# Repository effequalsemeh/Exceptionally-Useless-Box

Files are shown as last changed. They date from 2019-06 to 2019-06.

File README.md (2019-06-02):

# Exceptionally-Useless-Box
All files related to building the Exceptionally Useless Box

See demonstration of the device working here: https://youtu.be/8gKpCouH2lw

There is only a rough guide for setting this thing up, and it's from the project report that was generated for this. Look at Documentation/MECH-457, Project Report, Reduced. I will upload a better schematic and assembly guide later on as time permits.

To-Do:
1. Upload schematic after drawing in Eagle/KiCad
2. Create a BOM
3. Upload a guide on assembly

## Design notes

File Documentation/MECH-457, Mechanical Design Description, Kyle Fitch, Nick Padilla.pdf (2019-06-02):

## Mechanical Design Description for the MECH-457 Project

### Exceptionally Useless Box

Note that a Solidworks model should be supplied with this document that these words are in reference to.

The project is housed in a 1/8th inch, laser-cut enclosure that facilitates mounting points for a toggle switch, ultrasonic proximity sensor, two different servo-arm assemblies, and hinged doors from which arms may egress. Hinging of the doors is accomplished with flush-mount piano hinges. Each servo assembly features a mount for connecting to the servo and chassis. The servo mount also features a bolt for a fixed pivot point where a 5-bar linkage (the arm) connects to. The servo mount provides limited adjustability in xyz directions for alignment purposes.

Power is supplied by a battery pack, which will be adhered to the inside of the enclosure using adhesivebacked hook-and-loop tape. Similarly, the breadboard for connecting the electronics is also adhered to the inside of the enclosure with the built-in adhesive backing where clearance allows. Lastly, a power switch is panel-mounted on the bottom for turning the device on and off.

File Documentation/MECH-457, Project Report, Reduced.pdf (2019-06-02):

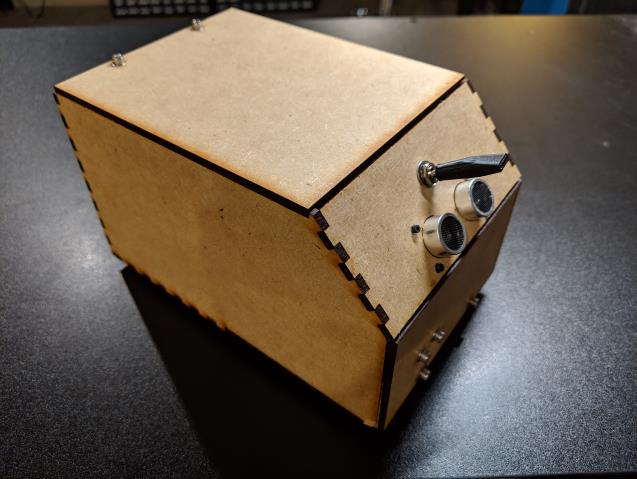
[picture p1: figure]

# Exceptionally Useless Box

Kyle Fitch

Nick Padilla

MECH 457/857

5/1/19

## Summary of Project

There is a novelty toy called a “useless box” where a box features a mounted switch that the

user toggles. Upon toggling the switch, something comes out of the box to toggle the switch back to the

original position. The goal of this project was to make an exceptionally useless box. In order to do this,

the user should not even get to toggle the switch in the first place. Therefore, the box needed to watch

for the user’s hand approaching and preemptively toggle the switch when the hand gets close enough

followed by the usual sequence of resetting the switch as in the original useless box design.

To detect the hand, the device features an ultrasonic sensor connected to an Arduino Pro Mini.

The microcontroller uses this input as a way to detect the proximity of the hand and translate that

distance into rotating a servo. In doing this, the servo motion “follows” the hand as it approaches or

backs off. Connected to this servo is an arm made up of a 5-bar linkage that when fully extended can

toggle the switch and similarly fully retract into the box. A second servo with another arm serves the

purpose of resetting the toggle switch once it has been engaged by the other arm.

The team hoped that such a simple concept would leave plenty of time to execute and perfect

complete mechanical and electrical designs with well-performing code. Unfortunately, with the

complexity involved in the 5-bar linkages, iterating the mechanical design took a large portion of the

semester. Since the mechanical design needed to be complete before tuning the coding, the

performance of the device was not able to be honed. However, the device in its present state meets our

expectations in its functionality and aesthetic appearance. Early on in the project, having the motion of

the servo follow the distance measurements made by the sensor was intended to be controlled with

PID. Currently, this function is performed instead by a mapping function and rolling average filter.

Future testing will be performed to implement PID control for much faster response and a reduction in

the jittery motion sometimes brought on by the sensor. Lastly, it would be ideal to make a circuit board

to get rid of the breadboard electronics which will reduce the amount of wiring inside the device and

thus reducing noise in the system.

## Table of Contents

Step 1 – Component Validation
Step 2 – Sensor wiring
Step 3 – Servo wiring
Step 4 – Toggle switch wiring
Step 5 – Microcontroller power wiring
Step 6 – Electronics testing
Step 7 – Mechanical design
Step 8 – Finished Project

### 1Component Validation

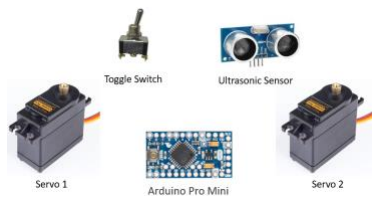
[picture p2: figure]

Component selection was straightforward in that they were already defined when the concept of the project was determined. It was known that two servos, one ultrasonic sensor, a toggle switch, microcontroller, power switch, and batteries would be necessary. An Arduino Pro Mini was chosen for the microcontroller since it was on hand through the lab materials of the MECH-457 course. The ultrasonic sensor that was selected was an HC-SR04 module, which are plentiful and cheap, and were curated through Amazon. The power switch and battery packs (for AA batteries) were already on hand and were used for the project. These components worked well and were used in the final project.

Originally, an SG90 micro servo was used in the design to drive the arms due to their small size. This proved to be a mistake as it not only had too low of torque, but the nylon servo horns that it came with were difficult to join the arms to. After observing this, larger servo motors were ordered that included standard teeth (25T) for the servo horn. These motors had 15 times the amount of torque that the micro servos had, so was clear that that problem would be solved. Because of the 25T tooth profile on the servo meant that a special, metal servo horns could be used to join the arms using threaded holes in the horn. This ended up being the perfect solution for converting the torque of the motor to the arms.

On the subject of torque, a larger toggle switch was originally purchased for having a longer lever to solve some clearance issues in the kinematics of the arms. Unfortunately, the force required to flip the toggle switch was very high and the housing behind the lever of the switch (the part that is hidden inside the enclosure) was too bulky and caused many different clearance issues. A mini toggle switch was then purchased which had a lower force to flip and was much smaller in size. A 3d printed part was designed to slip onto the lever for increasing the length of the lever as well, which lowered the force needed to toggle the switch even further.

The enclosure was intended to be laser cut from 0.125” material and would be appropriate regardless of the type of material (that can be cut with a low power laser) since the joints would be bolted connections and finger joints with an adhesive. For this project, MDF was used because it was low in cost and easy to cut on the laser with reliable, flat surfaces that did not warp during the manufacturing process. However, Delrin was used for the linkages for their high strength and rigidity. Delrin also cuts well on the laser, but with larger parts, it can have some warping. This was not an issue, however, since the linkages were quite small.

The mounts of the servo motors and arm were originally made from MDF, but after prototyping, it was obvious that it would not be rigid enough, so Delrin was also used for these parts as well. The pins that were used for joining the arm linkages were machined from 1/8” stainless rod stock since they were non-standard lengths. Retaining the linkages on the pins were friction-based snap ring clips, which allowed for adjustment in the amount of play between the linkages. Another benefit to using Delrin for the linkages was the material’s low coefficient of friction, which kept the linkages from binding throughout their motion.

All fasteners involved in the project were determined during the modeling process and ordered from McMaster-Carr when the design was ready. Finally, piano hinge material was used to join the top and front “doors” to the enclosure.

### 2Sensor Wiring

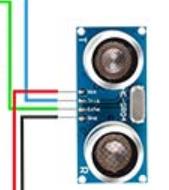
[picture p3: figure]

Wiring an ultrasonic sensor is straightforward and is made even easier with a datasheet provided by the manufacturer. There are 4 pins: input voltage (VCC), ground (GND), trigger (TRIG), and echo (ECHO). Voltage from the “RAW” pin of the microcontroller was connected to VCC. GND on the sensor was connected to the GND of the microcontroller. TRIG and ECHO pins needed to be connected to any digital pin, which for this project were pins 6 and 7, respectively.

Most manufacturers of the HC-SR04 also provide the equation that is needed to calculate the distance from the readings of the sensor. So, it was not necessary to determine this ourselves.

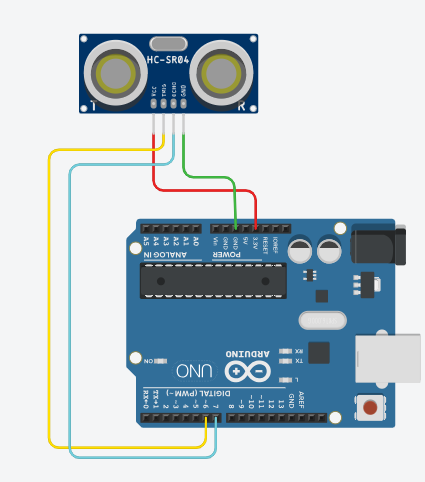
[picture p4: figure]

### 3Servo Wiring

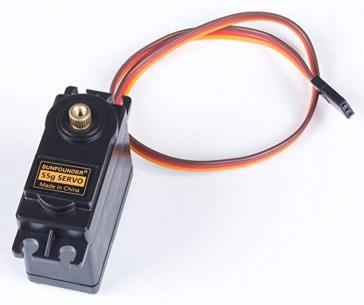
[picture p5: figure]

Servos typically have just three leads to connect; input voltage, ground, and signal. The respective wires will vary from motor to motor, so consulting the datasheet was be necessary to determine which lead is what. For this project, the red wire was Vin, the brown wire was GND, and the yellow wire was signal. It was important to connect the Vin and GND wires to a separate power supply than the one that powers the microcontroller. This avoided frustrating noise issues that are difficult to troubleshoot. The magnitude of the input voltage also varies from motor to motor and must be sought out from the datasheet. For this motor, 6V were required with up to 2A of current. So, a battery pack with four AA batteries connected in series were connected to the Vin and GND wires of the servo motors. The signal pins for each motor were then connected to a PWM-enabled digital pin on the microcontroller (pin 10 for the bottom arm servo, pin 11 for the top arm servo). A rocker switch was also connected between the series circuit of the batteries and servos to control when the motors were given power.

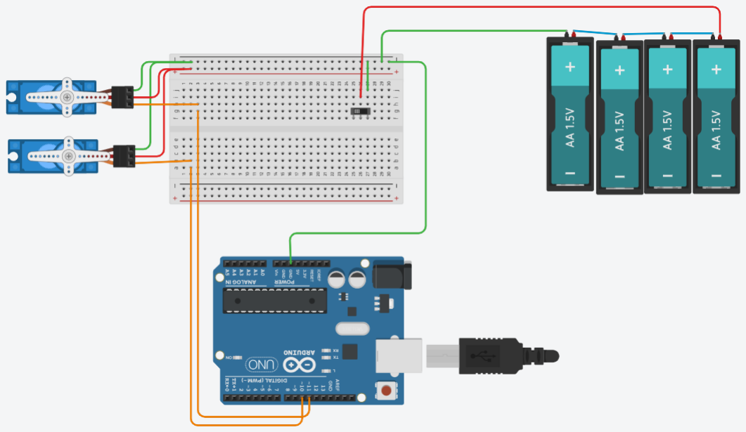
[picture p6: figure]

### 4Toggle Switch Wiring

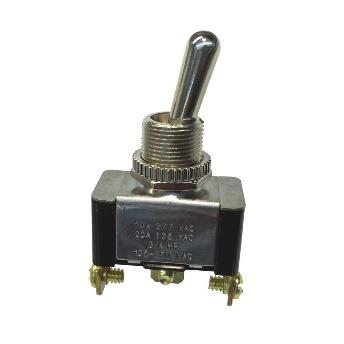
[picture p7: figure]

The toggle switch that was to be flipped back and forth by the device was connected from a digital pin (pin 5 for this project) to the GND pin of the microcontroller. Since the switch would be normally open, a pull-up resistor was required from the digital pin to the 3.3V output of the microcontroller. The value of this resistor was mostly arbitrary barring abnormally high or low resistances. A 10 kΩ resistor was used for this project.

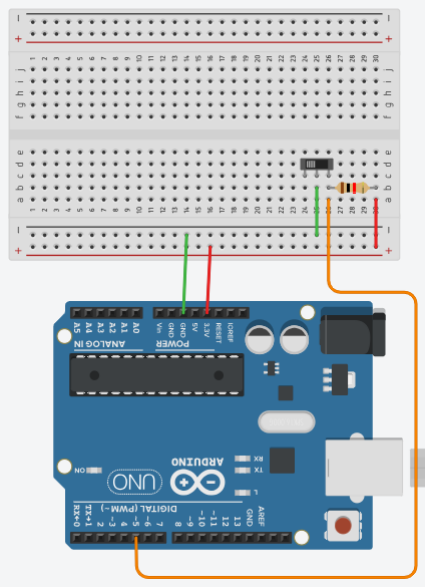
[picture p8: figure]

### 5Microcontroller Power Wiring

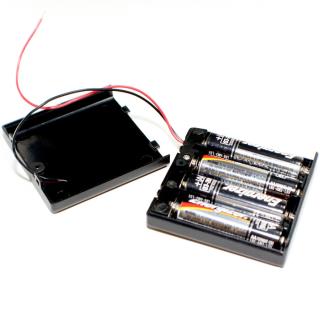
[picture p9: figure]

The microcontroller needed to be supplied with a separate power supply from the servo motors as indicated in step 4. From the datasheet, the input voltage for the microcontroller would need be from 3.3V to 12V. So, another 4 AA batteries were placed into a battery pack whose leads were then connected to the RAW pin (positive side of battery terminals) and GND pin of the microcontroller.

As was done before, another switch was placed between the positive lead of the battery pack and the RAW pin. This would allow for independent power cycling of the microcontroller and sensor so that the device could be unpowered when not in use. It was also useful to be able to power the microcontroller without the servos activated so that if code that was previously uploaded and caused crashes, it could be safely rectified.

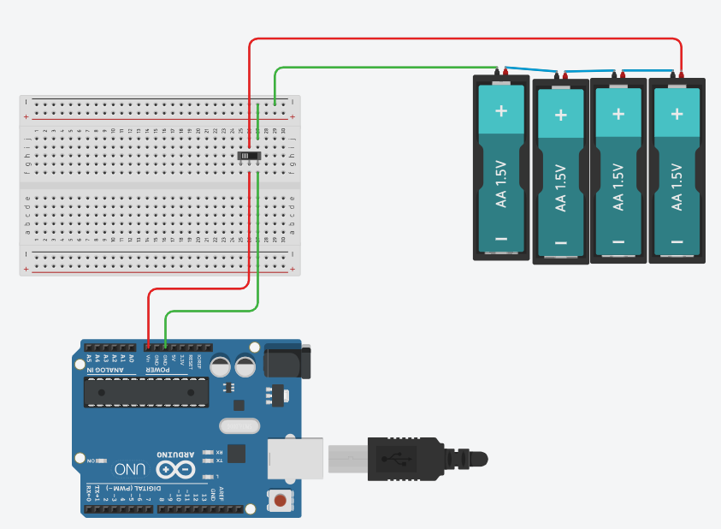
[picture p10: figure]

### 6Electronics Testing

With the electronics connected, they were tested before
assembling into the enclosure itself. Prototyped code was uploaded

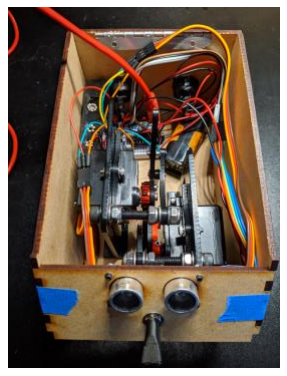
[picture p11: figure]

to the microcontroller using the Arduino IDE. It was important to ensure that the correct processor is selected before uploading. This caused for some headache when initially working with this board. For this project, we used the 3.3V 8 MHz version of the Arduino Pro Mini.

With the code uploaded, we pointed the sensor in a direction with a lot of space. Some noise was heard from the servos when the program loads, indicating that they were energized. Then, a hand was placed in front of and a couple feet from the sensor and slowly approached the sensor. The bottom then rotated as the hand became closer to the sensor. When the hand was close enough, the servo suddenly moved, and both servos remained still thereafter. After flipping the switch one direction, the other (top) servo was observed rotating. After flipping the switch in the other direction, the top servo rotated once again. Finally, the bottom servo was again responding to input from the ultrasonic sensor.

### 7Mechanical Design

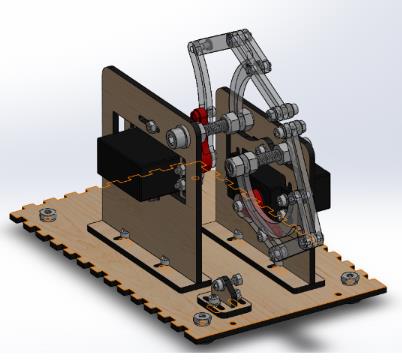
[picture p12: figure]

The most difficult part of the design in this project was being able to fit the servos as close to the switch as possible. Because the arms needed to contact the switch directly in line (such that they were both rotating or moving in the same plane), both servos could not be positioned in the same place with respect to the switch. To avoid this headache, one could simply position them in the same place yet separated along their axes of rotation far enough away to give clearance for the arms and at the end of either arm, a perpendicular piece to contact the switch lever with could be added. However, this would add a much larger torque to the linkages and rigidity issues will have arisen when attempting to make such a small form factor. It is this fact that there were two servos instead of one that made this project exceptionally challenging.

The mechanical design was begun by modeling the switch and fixing it in a position that was indicative to where it will be in the final design. Using circles as guides, the best combinations of lengths for the 5-bar linkage were experimentally determined until the end of the arm that meets the switch could fully retract into what would be the enclosure as well as extending a good amount of distance past the toggle switch so that flexure in the parts could be compensated for. This was where most of the time was spent in the design. It was important to give plenty of room for everything. The more that the size of the enclosure was limited, the more difficulty there was in designing the linkages. This process was done for the bottom arm only. The top arm was dependent on the physical size and shape of the bottom arm and required its complete model before designing the top arm linkage.

With the bottom linkage prepared, a mount that can hold the servo with adjustability in the translation of the servo in all three axes was modeled. Doing this allowed for adjustability in the actual prototype to make up for defects and ended up being extremely useful. The mount itself was the ground for the 5-bar linkage and allowed for adjustability in the positions of the two ground points with respect to one another. The mount was designed for rigidity where possible, knowing that a torque will be placed on the ground points.

Once an adjustable servo mount had been designed, the enclosure was modeled for affixing the mount, toggle switch, and ultrasonic sensor. The sensor needed to be positioned so that it is pointed where the user would be. It was important to not let the arms interfere with the sensor measurements as well. One thing that was not accounted for in our design was an angular adjustability in the ultrasonic sensor. While a 45 degree angle with respect to the surface that the device rested on worked, a lower angle would have resulted in better distance measurements since the hand tends to approach the device from an angle more directly in front of it, rather than above.

With the sensor and bottom servo arm mechanism mounted and fixed in place, the top arm to toggle the switch back was designed using the same procedure as was done with the bottom arm. It was critical to keep track of where the bottom arm will be during all points of its rotation so that the top arm can always perform without interference. A lot of time was spent here as well since the clearances for everything were very difficult to determine until complete models were made whose motions could be observed in an assembly to inspect for flaws.

Some way to retract the front door was also necessary. A tension spring was used for this project, but a torsion spring could have been used, but it was more trivial to find joinery that would easily accommodate the tension spring. The top door automatically closed by virtue of its own weight, so a return mechanism was not needed. A way to join the hinges to the enclosure and both doors was also be necessary. For this project, holes were drilled in the hinges and then bolted to their respective pieces. Modeling was also necessary for this feature as well because slots in the enclosure parts were needed for bolt clearances that
accommodated some tolerancing in the hinge’s position.

When designing the enclosure, enough room was needed to be made for not only the servo arm subassemblies, but also for the electronics. Room was accommodated for a mini breadboard with 2 battery packs and means for mounting the two power switches. Lastly, this project did not include an access panel for changing batteries, but would have been beneficial to include for the lifetime of the product when battery changes were needed.

Since the majority of the mechanical parts were to be laser cut, it was extremely useful to have the entire product modeled (excepting the microcontroller, breadboard, and wiring). In doing this, changes to the design could quickly be made, verified, exported to a laser job file, and fabricated. Modeling in this way was most likely critical to the success of this design because of the amount of iteration that was involved in prototyping.

When the parts were completely modeled, the prototype was assembled without the front and top doors attached. Some simple code to extend and retract each arm one by one was uploaded. While observing the motion of the links, adjustments were made to the servo mounts positions with respect to the toggle switch until both arms were reliably toggling the switch lever. At the same time, the exact angle limits of each servo were experimentally determined by adjusting their values in the code. When it was confirmed that the arms were completely retracted without striking each other and that both arms could flip the toggle switch, the doors were assembled and the hinges adjusted to allow the doors to completely close without interference. Similarly, tension on the spring of the return mechanism for the front door was adjusted by sliding the spring’s mounting point further away so that the front door would completely close.

### 8Finished Project

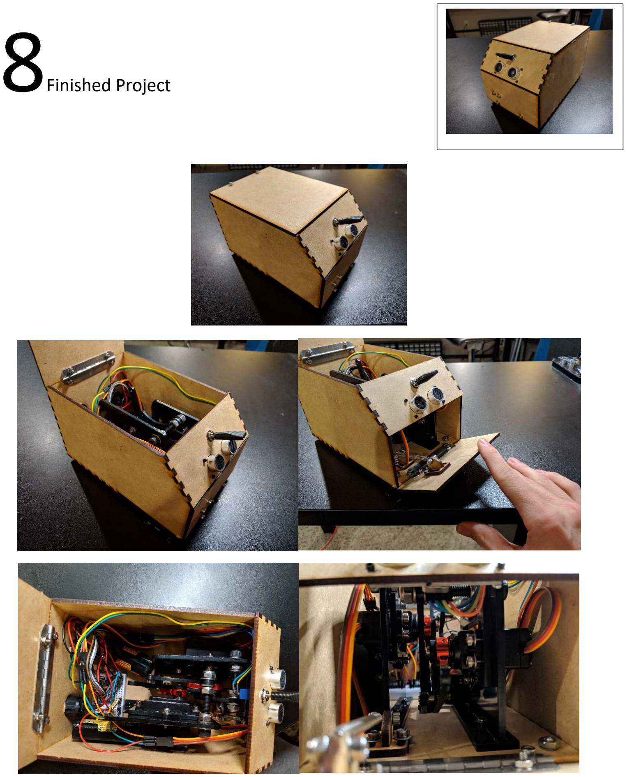
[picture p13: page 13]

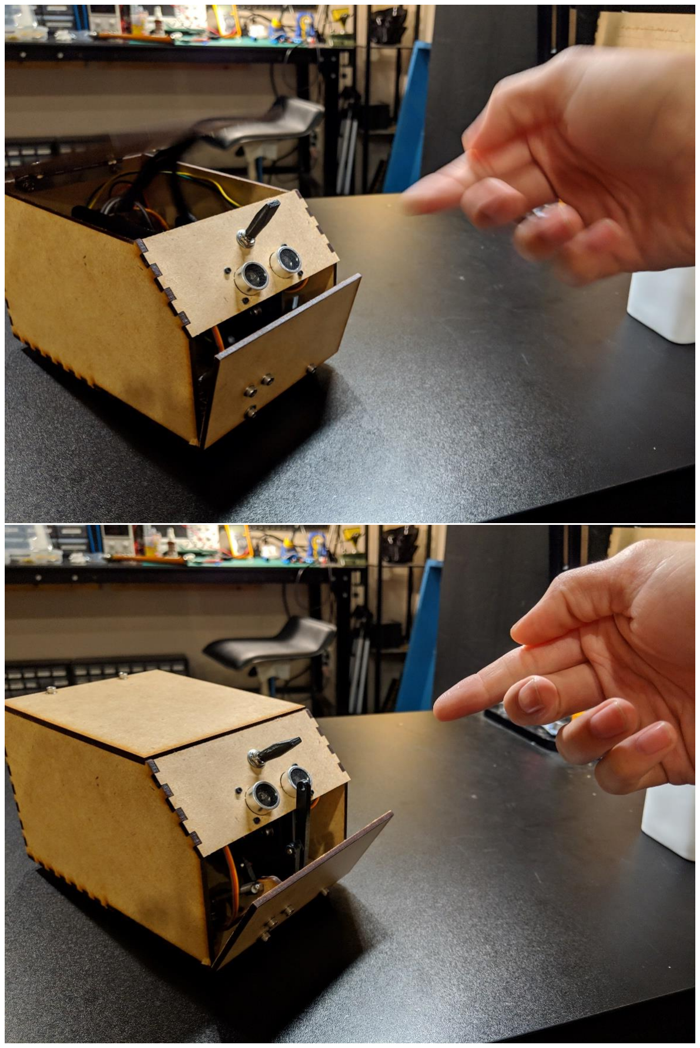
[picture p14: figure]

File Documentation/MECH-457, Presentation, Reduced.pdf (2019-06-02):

# Exceptionally Useless Box

## KYLE FITCH

## NICK PADILLA

# Motivation/Background

# This is a useless box

But it’s not really that useless…

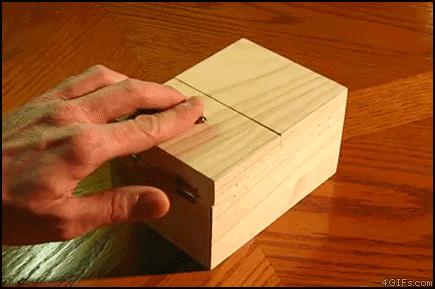
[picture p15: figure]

# HOW DO WE MAKE A BOX THAT IS EXCEPTIONALLY USELESS?!

# THE EXCEPTIONALLY USELESS BOX

Remove the interaction of the user with the box altogether
- The box flips the switch itself when a hand approaches
- Then the box flips it back like normal

Components:
- Arduino
- Ultrasonic sensor (measure distance of hand)
- 2 servos
- Toggle switch

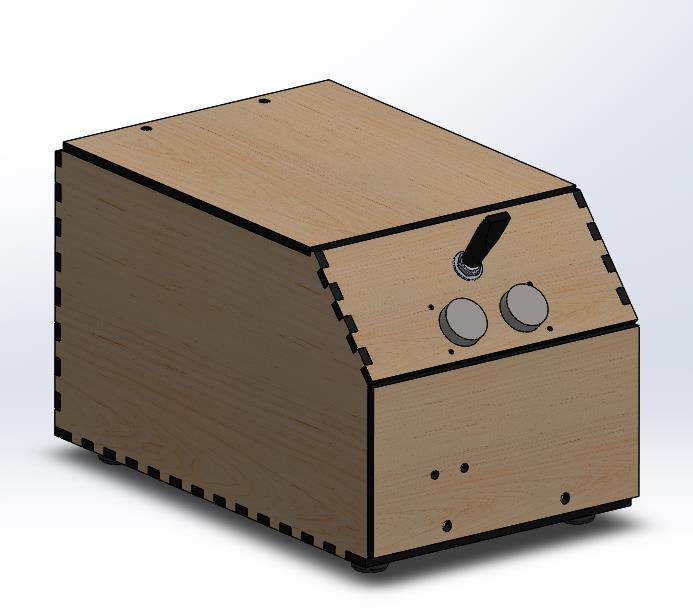
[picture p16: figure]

How can a robot have a purpose when you take it away?

# Calculation Components

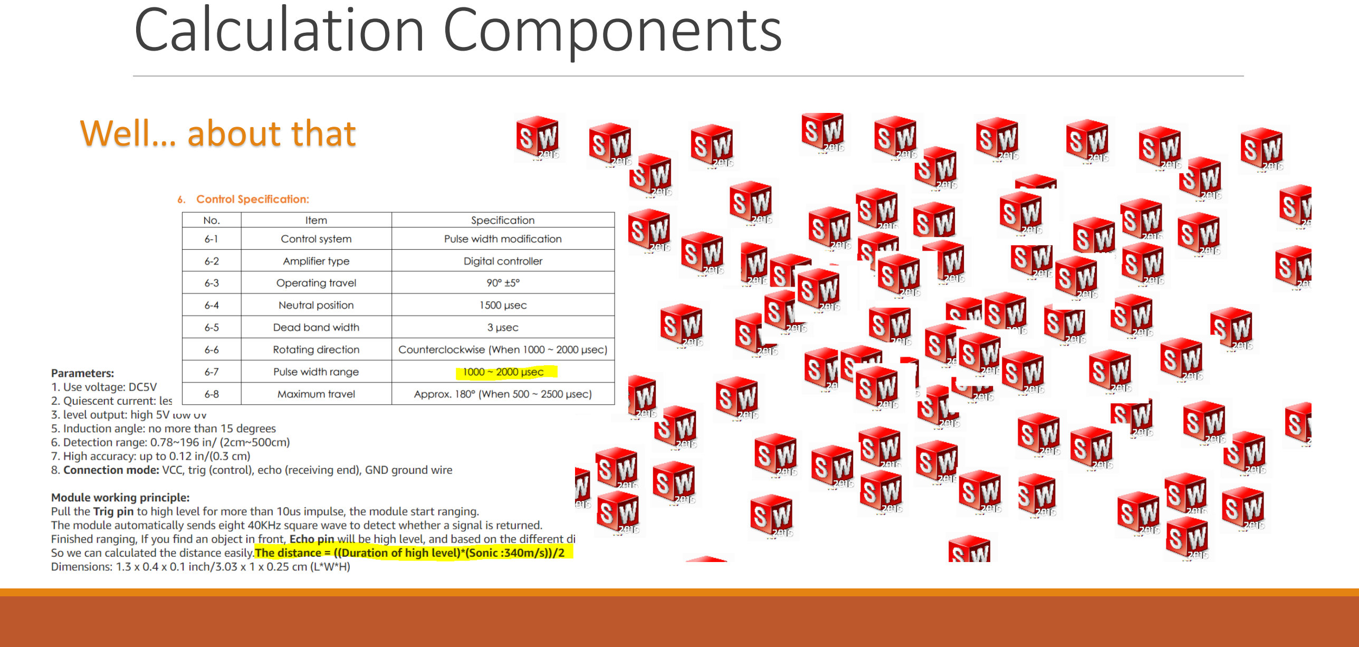
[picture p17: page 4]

## Well… about that

# Calculation Components (2)

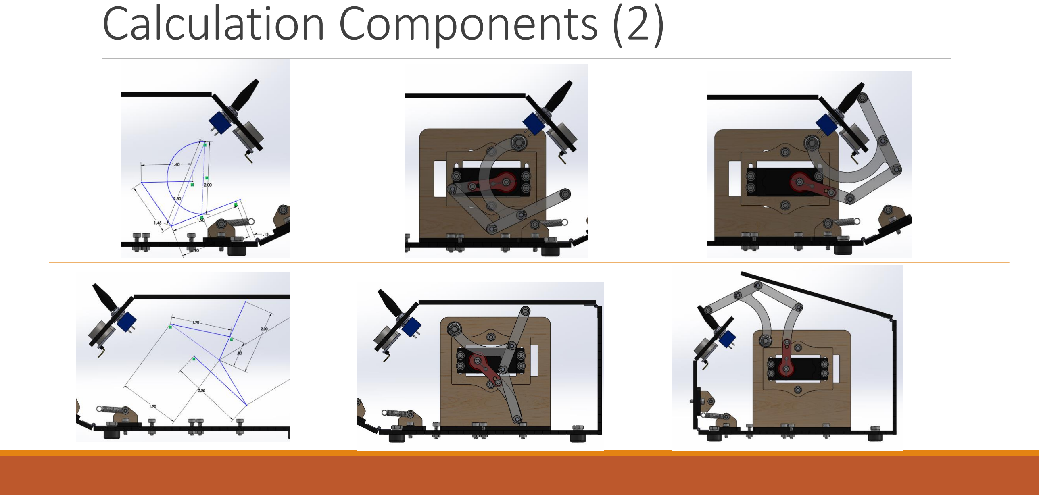
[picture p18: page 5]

# Calculation Components (3)

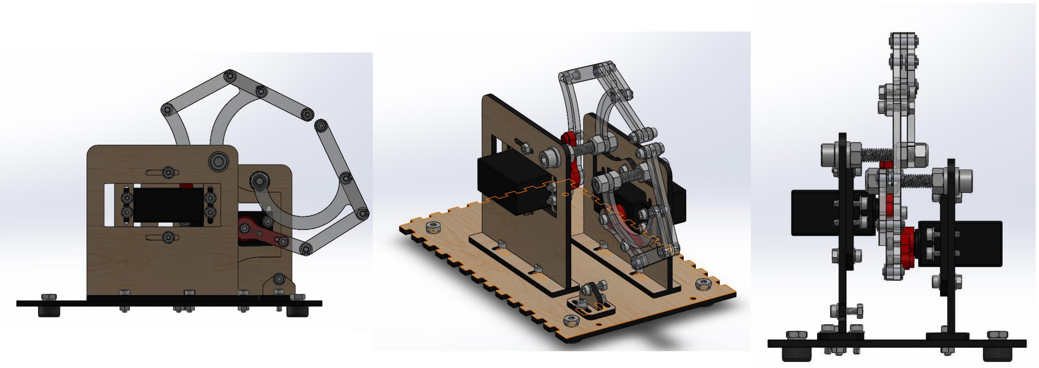
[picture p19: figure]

# Mechanical Components/Design

Enclosure
- Laser cut chassis, 1/8” MDF & Delrin
- Piano hinges w/ spring return on front door
- Lots of M3 hardware

Servo Arm mechanisms
- Laser cut Delrin links
- 1/8” pins with friction-fit spring clips
- Adjustable mount

# Electronic Components/Design

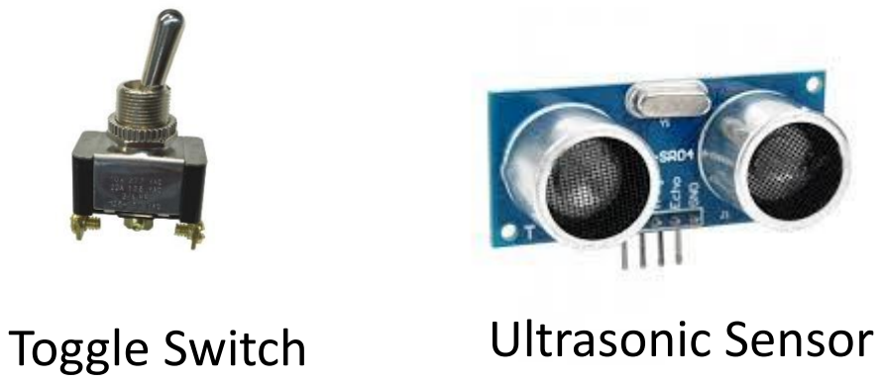
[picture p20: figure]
Toggle Switch; Ultrasonic Sensor
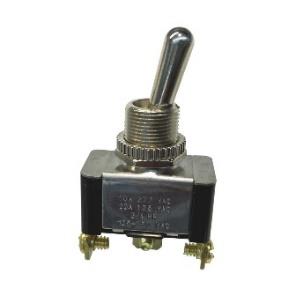
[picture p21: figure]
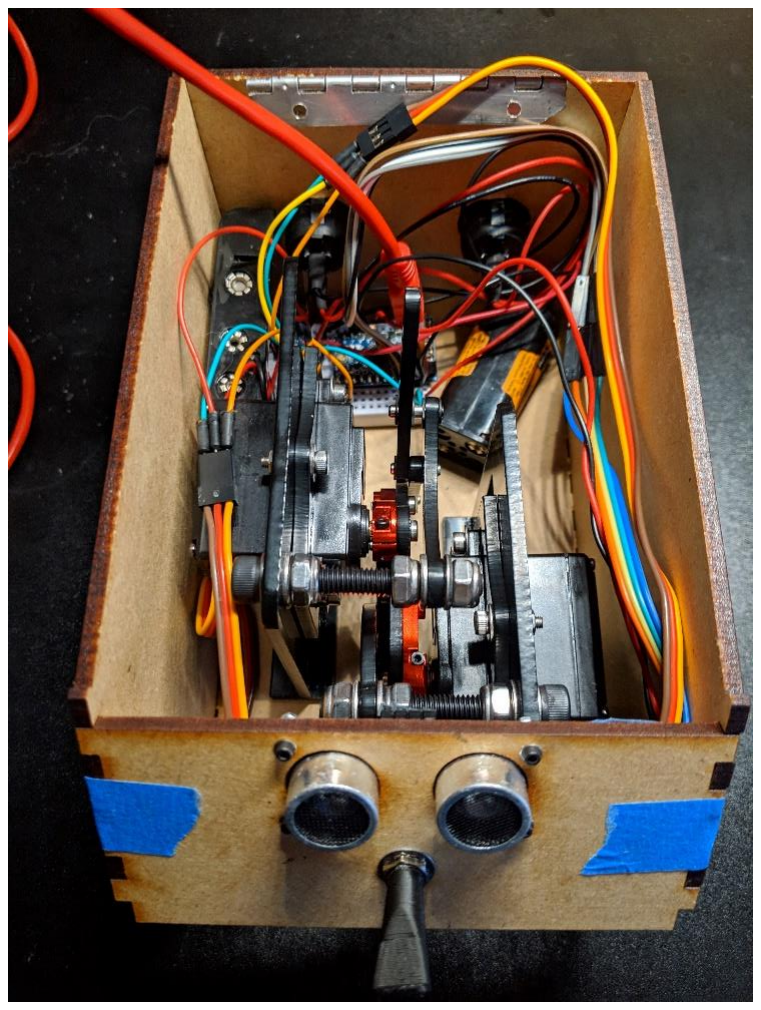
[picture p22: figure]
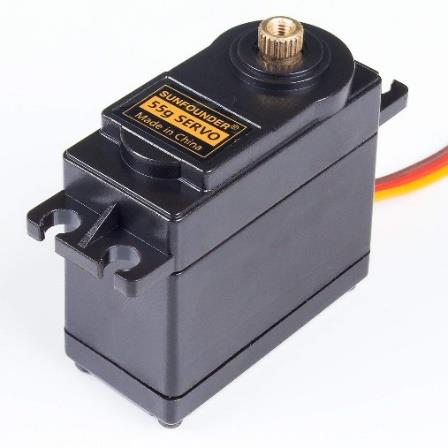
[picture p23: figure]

2 Servo
Motors

## And a LOT of electron spaghetti

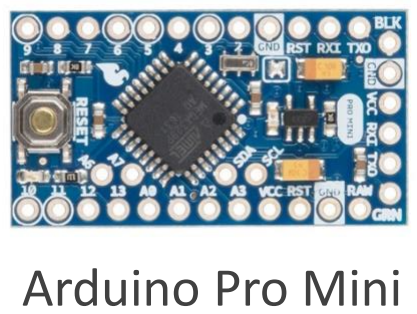
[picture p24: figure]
Arduino Pro Mini

# System Control/Programming

Distance Measurement; Map to servo Output angle; Rolling Average Filter; Flip the switch; Is the hand close?; Nope; Yep

# Demonstration

# Group Member Contribution

Kyle Fitch: Mechanical design, electrical design

Nick Padilla: Programming

McMaster Carr: Modeled all our fasteners, washers, nuts, rubber bumpers, snap rings, etc. Always delivered what we asked for in a day, always available to give us a part model, never argued. 10/10 group member, would recommend.

# PEAK USELESSNESS AT MINIMUM EFFICIENCY

# Questions?

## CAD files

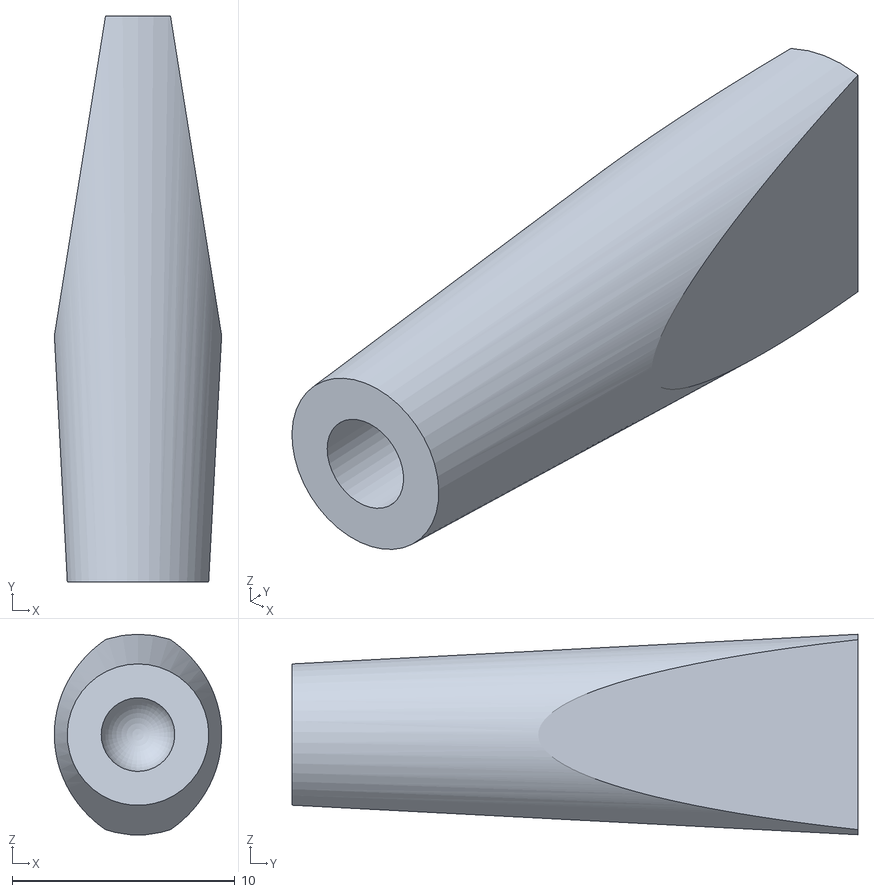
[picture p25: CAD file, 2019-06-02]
3d Printing Files/Small Switch, Lever Cover.STL
7.51 x 25.4 x 9.00

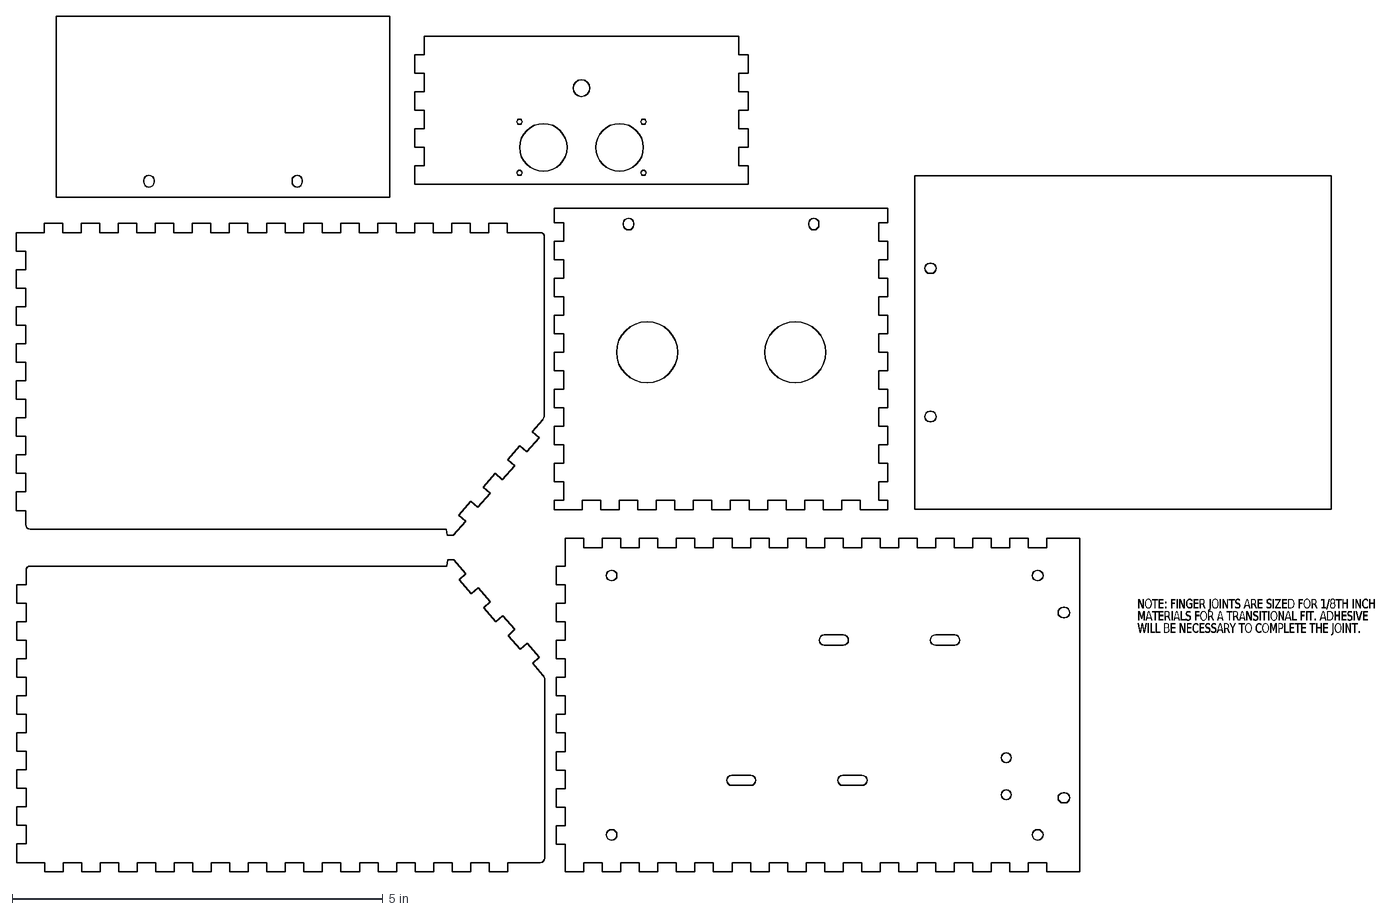
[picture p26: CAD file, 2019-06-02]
Laser Cutting Files/Enclosure Laser Cut Layout.DXF
NOTE: FINGER JOINTS ARE SIZED FOR 1/8TH INCH
MATERIALS FOR A TRANSITIONAL FIT. ADHESIVE
WILL BE NECESSARY TO COMPLETE THE JOINT.

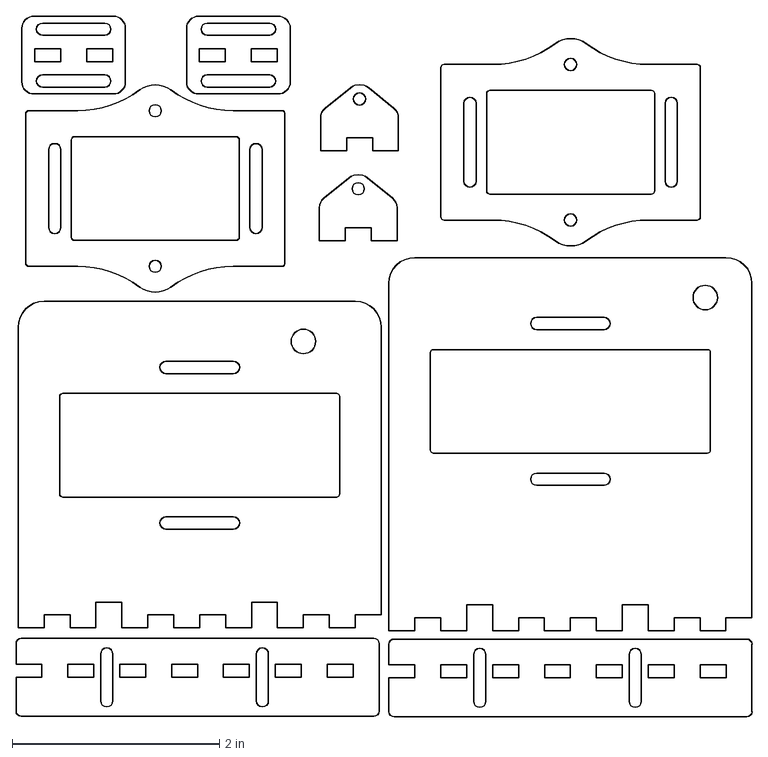
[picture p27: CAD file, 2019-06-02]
Laser Cutting Files/Servo Mount Laser Cut Layout.DXF
7.09 x 6.75 in

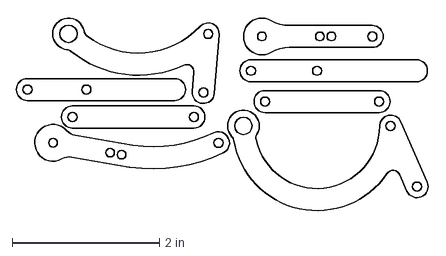
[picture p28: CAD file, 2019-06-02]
Laser Cutting Files/Linkage Laser Cut Layout.DXF
5.62 x 2.72 in

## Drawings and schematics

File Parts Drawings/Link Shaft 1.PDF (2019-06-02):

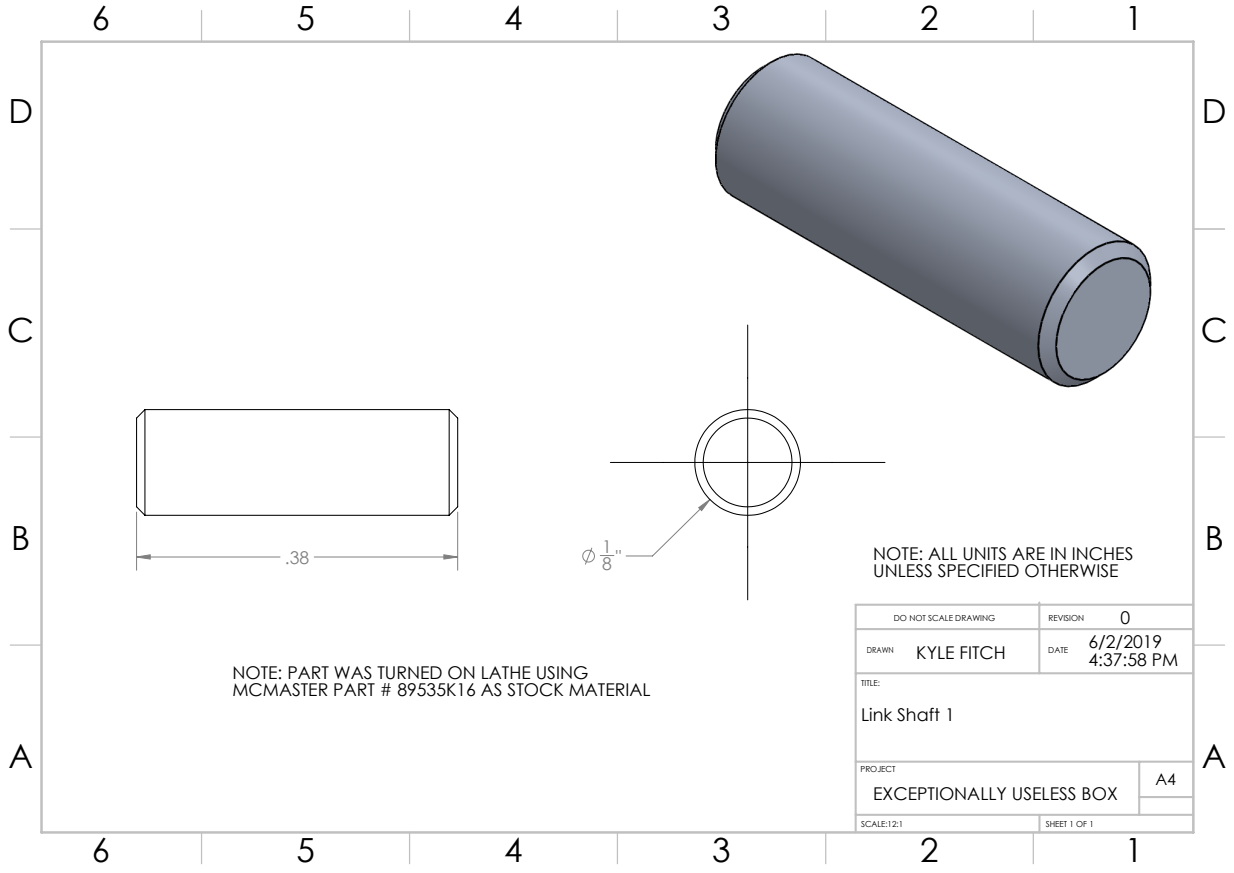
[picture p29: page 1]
NOTE: ALL UNITS ARE IN INCHES; SCALE:12:1; SHEET 1 OF 1; Link Shaft 1

UNLESS SPECIFIED OTHERWISE

DO NOT SCALE DRAWING | 0 REVISION

KYLE FITCH DRAWN | 6/2/2019 DATE 4:37:58 PM

NOTE: PART WAS TURNED ON LATHE USING
MCMASTER PART # 89535K16 AS STOCK MATERIAL

PROJECT
EXCEPTIONALLY USELESS BOX

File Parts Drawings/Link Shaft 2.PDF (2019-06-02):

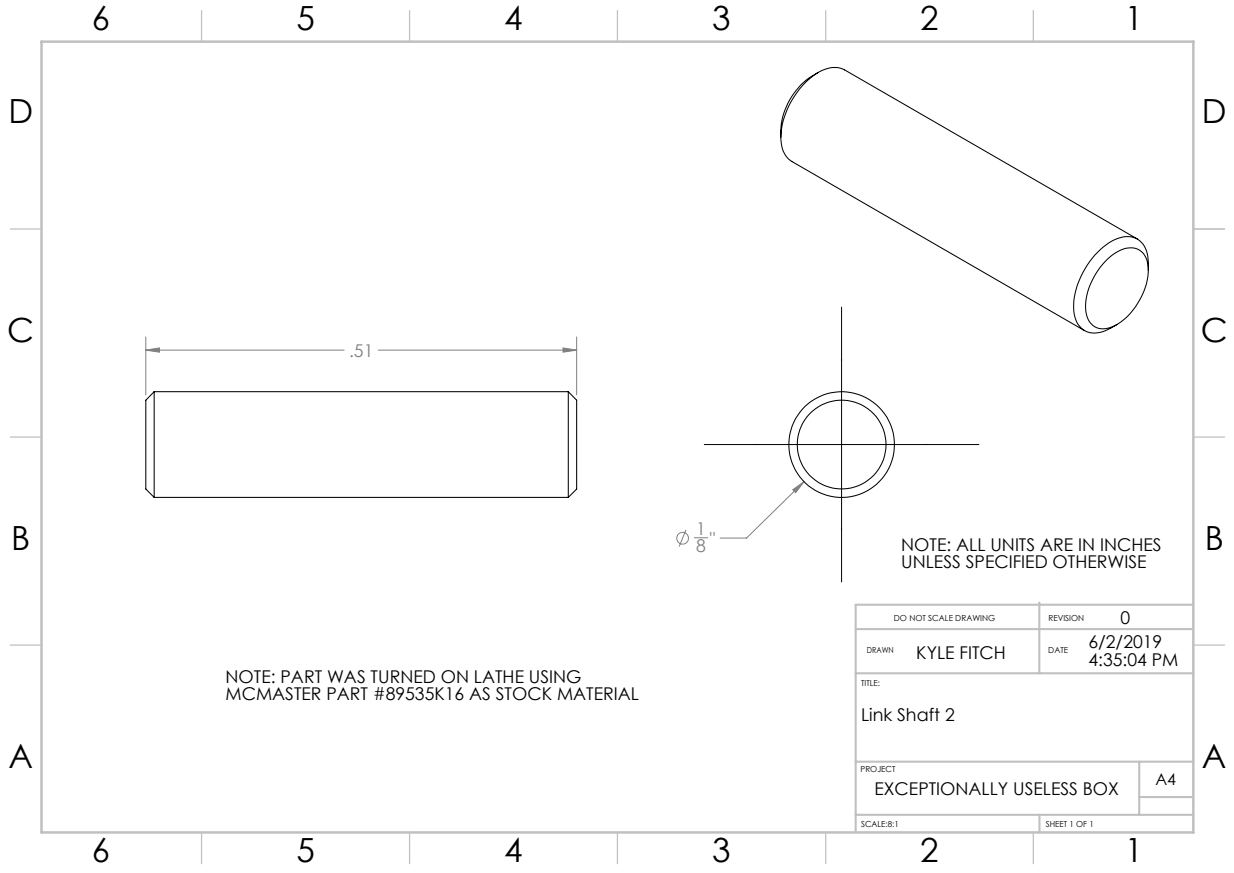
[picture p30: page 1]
NOTE: ALL UNITS ARE IN INCHES; SCALE:8:1; SHEET 1 OF 1; Link Shaft 2

UNLESS SPECIFIED OTHERWISE

DO NOT SCALE DRAWING | 0 REVISION

KYLE FITCH DRAWN | 6/2/2019 DATE 4:35:04 PM

NOTE: PART WAS TURNED ON LATHE USING
MCMASTER PART #89535K16 AS STOCK MATERIAL

PROJECT
EXCEPTIONALLY USELESS BOX

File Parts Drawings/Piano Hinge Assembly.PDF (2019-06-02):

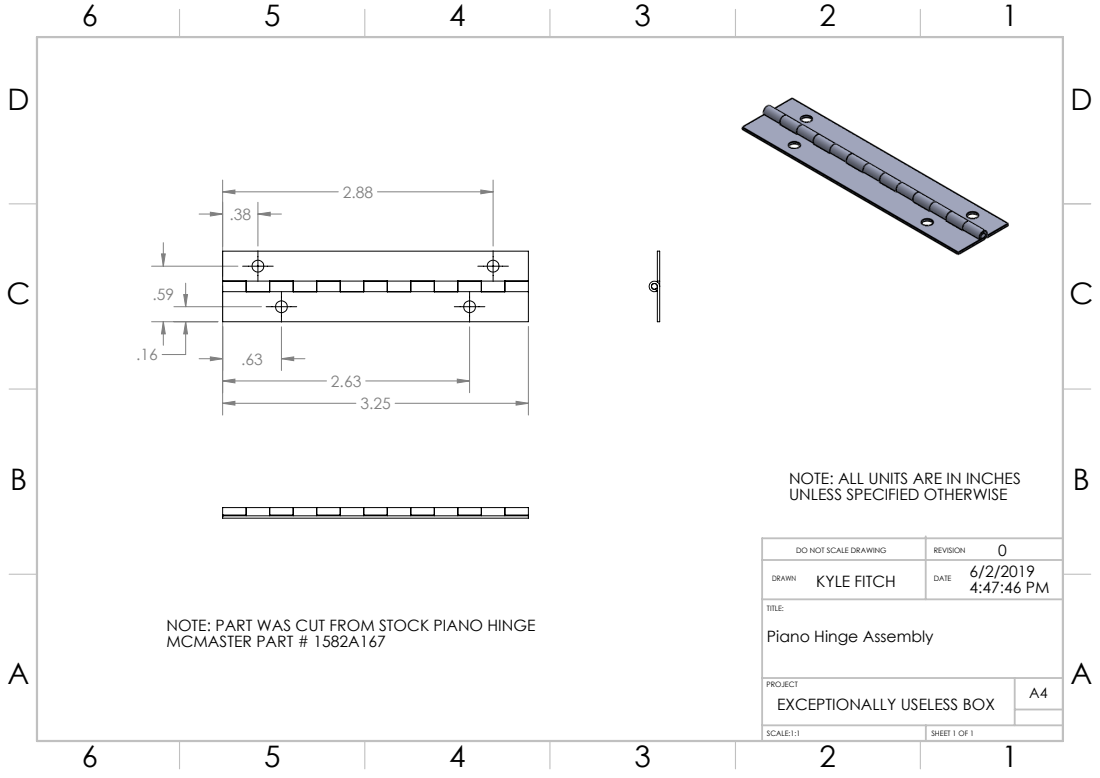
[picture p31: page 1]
SCALE:1:1; SHEET 1 OF 1

NOTE: ALL UNITS ARE IN INCHES
UNLESS SPECIFIED OTHERWISE

DO NOT SCALE DRAWING | 0 REVISION

KYLE FITCH DRAWN | 6/2/2019 DATE 4:47:46 PM

TITLE:
Piano Hinge Assembly

NOTE: PART WAS CUT FROM STOCK PIANO HINGE
MCMASTER PART # 1582A167

PROJECT
EXCEPTIONALLY USELESS BOX

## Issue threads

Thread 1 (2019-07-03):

clarification

dmbigalke, 2019-07-03:
I am looking to build this as it looks like a fun project. In review the documentation you have, you mention you used a Pro Mini board but your diagrams have an Uno to show the pinouts. Which did you use? Can you use either board?

RobertJoanne, 2020-02-21:
I would also like to build this, but I need the scale for the DXF files so I can get them cut.  Can anyone help?

colaplate, 2021-01-23:
> 我也想构建它，但是我需要DXF文件的比例，以便将它们剪切。有人可以帮忙吗？

There is indeed a proportional problem. After wasting a few sets of materials, I repaired the production file according to the screw specifications. I am not sure how to submit the update, but you can send it to you after providing the email.

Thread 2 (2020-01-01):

3D-printed box

RFL91, 2020-01-01:
nice work! I am an absolute beginner with arduino. Could you upload files to print these wooden parts?

JybOlrp, 2021-03-13:
I've converted the DXF lasercutting drawings to STL. Scaling the model during import in FreeCAD was a bit tricky, but got it covered. Distance sensor fits like a glove into the plate.
[Exceptionally-Useless-Box_STL_box.zip](https://github.com/effequalsemeh/Exceptionally-Useless-Box/files/6134333/Exceptionally-Useless-Box_STL_box.zip)

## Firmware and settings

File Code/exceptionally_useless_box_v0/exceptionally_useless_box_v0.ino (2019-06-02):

///////////////////////////////////////////////////////////////////////////////////////////////////////////////////
// This code is for The Exceptionally Useless Box. Currently set up to be run on an Arduino Pro Mini.
// Written by: Kyle Fitch
///////////////////////////////////////////////////////////////////////////////////////////////////////////////////
// Related project files are hosted on this repository: https://github.com/effequalsemeh/Exceptionally-Useless-Box
//////////////////////////////////////////////////////////////////////////////////////////////////////////////////
// Version History:
// 6-2-19 v0: initial release
//////////////////////////////////////////////////////////////////////////////////////////////////////////////////
// A note on using this code:
// When I wrote this, I did so in 30 minutes just to get it working. There are far more efficient ways to go about this,
// but this was the quickest and dirtiest way I could get it up and running. When the device is mechanically set up and in
// position, the botAngleMax, botAngleMin, topAngleMax, and topAngleMin need to be tuned to dial in on how hard the arms need
// to press the switch and toggle it over.

#include <Servo.h>

const int switchPin = 5; // pin that the toggle switch is connected to
const int trigPin = 6; // "trig" pin on the ultrasonic sensor
const int echoPin = 7; // "echo" pin on the ultrasonic sensor
Servo topServo; // the "top" servo is the one whose arms extend out of the top lid
Servo botServo; // the "bot" or bottom servo is the one whose arms extend out of the front lid

float distance = 0; // variable to store the measured distance from the ultrasonic sensor
int switchState = 0; // variable to store the state of the switch
boolean switching = false; // used to control the state of the device and handle the delay of the servo rotation

const int botAngleMax=7;                 //angle in degrees that the bottom arm will fully extend to
const int botAngleMin=180;        // angle in degrees that the bottom arm goes to when fully retracted
const int topAngleMax=18;                //angle in degrees that the top arm will fully extend to        
const int topAngleMin=170;               //angle in degrees that the top arm goes to when fully retracted
const int distanceMax=50;                //the maximum distance away from the sensor that the bottom servo will respond to
const float thresholdPercent = 0.93; // percentage of the maximum travel of the bottom arm where the arm should fully commit to pressing the switch
const float threshCommit = thresholdPercent * botAngleMin; // the calculated angle when the arm should fully commit to pressing the switch


void setup() 
{
  topServo.attach(11);              
  botServo.attach(10);              
  topServo.write(topAngleMin);        //set initial position of the top arm
  botServo.write(botAngleMin);       //set initial position of the bottom arm
  pinMode(switchPin, INPUT_PULLUP); // don't forget to put a pull-up resistor on this pin
  pinMode(echoPin, INPUT);
  pinMode(trigPin, OUTPUT);
  Serial.begin(9600);
  Serial.println("Device is ready");

  // if the switch was already on when the device powers on, turn the switch off before entering the main loop
  if (digitalRead(switchPin)==HIGH && switchState == 0) // check if the switch is turned on when it was previously off
  {
    Serial.println("Upon boot, the switch was seen as turned on. Resetting it...");
    switching = true;
    switchState = 1;
    topServo.write(topAngleMax); // set position of top arm to hit the switch back off
    botServo.write(botAngleMin); // retract the bottom arm while the top arm turns the switch off
    while (switching == true) // don't do anything except wait for the arm to hit the switch 
    {
      if (digitalRead(switchPin) == LOW) // check if the switch is off yet
      {
        switchState = 0;
        switching = false;
        topServo.write(topAngleMin); // retract the top arm now that the switch is off
      }
    }
  }
  Serial.println("Starting the main loop");
}

void loop() 
{
  if (digitalRead(switchPin) == HIGH) // check if the switch was changed by the user before the bottom arm could do it
  {
    Serial.println("The switch was toggled before device was able to do it");
    switching = true;
    resetSwitch(); 
  }
  distance = getDistance();
  if (distance < distanceMax) // if the reading is close enough to the device, update the motor position
  {
    updateBotArm(distance);
    delay(15);                                                                                                                                            
  }
  else
  {
    botServo.write(botAngleMin); // retract the bottom arm if there's nothing in the way of the sensor
  }
}

int getDistance()
{                                                                                                                               
  digitalWrite(trigPin, LOW);
  delayMicroseconds(5);
  digitalWrite(trigPin, HIGH);
  delayMicroseconds(10);
  digitalWrite(trigPin,LOW);
  float duration = pulseIn(echoPin, HIGH);
  float measuredDistance = duration*.034/2;                                                                       
  return measuredDistance;
}


void updateBotArm(int handDistance)
{
  float motorPosition = map(handDistance, 0, distanceMax, botAngleMax, botAngleMin); // convert the sensor distance range to the output angle range, but inverted so that the angle goes up as the distance goes down
      Serial.print(distance);
    Serial.print(", ");
    Serial.println(motorPosition);
  {
    if (distance < 7)
    {
      commit();
    }
    else
    {
      botServo.write(motorPosition);
    }
  }
}

void commit()
{
  Serial.println("Committing to pressing the switch...");
  botServo.write(botAngleMax);
  while (switchState == 0)
  {
    if (digitalRead(switchPin) == HIGH)
    {
      switchState = 1;
      switching = true;
      botServo.write(botAngleMin);
      Serial.println("Switch has been toggled by the bottom arm");
    }
  }
  resetSwitch();
}

void resetSwitch()
{
  Serial.println("Resetting switch...");
  topServo.write(topAngleMax); // set position of top arm to hit the switch back off
  while (switching == true) // don't do anything except wait for the arm to hit the switch 
  {
    if (digitalRead(switchPin) == LOW) // check if the switch is off yet
    {
      switchState = 0;
      switching = false;
      topServo.write(topAngleMin); // retract the top arm now that the switch is off
      Serial.println("Switch has been toggled back by the top arm");
    }
  }
  Serial.println("Switch should be reset now");
}
